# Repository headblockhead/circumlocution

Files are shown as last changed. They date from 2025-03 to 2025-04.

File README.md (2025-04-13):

# Circumlocution

> the use of many words where fewer would do, especially in a deliberate attempt to be vague or evasive.

Welcome to maker hell, where we have all the parts of a broken Ender 3 clone, none of the time, a copy of FreeCAD, and an unhinged desire to watch an overcomplicated 3D printer spin.

## Build Guide

You should not build this printer. That's probably not something you would usually read in a project's README, but it's true.

I designed this printer to make something out of the assorted scraps of parts and frame left over from a dissasembled Sovol SV01 (Ender 3 clone with direct drive), and ideally something that looked funny or cool, hence the spinning bed. 

99% of decisions were based on what I had, or what I could buy cheaply, so some part selections or fastener choices are very strange.

If you also have some random Ender 3 related printer parts around the place, this project might work for you, but I guarentee that you will need to change some elements of the design, and you are best off making something else with the parts.

## How? Why?

1. Around 50 hours of hard work
2. Because I thought it would be funny, and I wanted to join in with [hackclub's infill project](https://github.com/hackclub/infill).

I chose FreeCAD because:
  1. I hate it when people's projects require people to beg/borrow/steal/leagally-buy Autodesk Fusion 360 access just to see or modify them
  2. I wanted to become more familliar with how FreeCAD works.

I may revise/re-make this project into something more complete with a followable build guide and a better design (EG. lots of X-space could be saved on the extruder design, a longer alu. extrusion could add a second Z axis, etc.) someday.

## CAD Gallery

Yes, the rectangular bed spins.

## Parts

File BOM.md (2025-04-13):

# BOM

(cables and fasteners not currently included)
(TODO: pricing)

- [ ] Turntable/lazy susan/bearing
- [ ] Orbiter v2.0
- [X] 4x NEMA 17 motors
- [X] 2x 5-8mm Z coupling
- [X] 2x 430mm(?) Lead screws
- [X] 2x lead screw nuts
- [X] 2x GT2 20tooth pulley
- [X] 1x MeanWell LRS-350
- [ ] 1x BLTouch
- [ ] 1x E3D v6 Hotend
- [ ] 2x 3010 fans (noctua?)
- [X] 1x SKR mini E3
- [X] 12x 2020 V-slot wheels
- [X] 2x 410mm 2040 extrusion (left+middle)
- [X] 2x 470mm 2040 extrusion (Z-axis)
- [X] 3x 400mm 2020 extrusion (top+bottom+X-axis)
- [X] 1x 450mm 2040 extrusion (right)

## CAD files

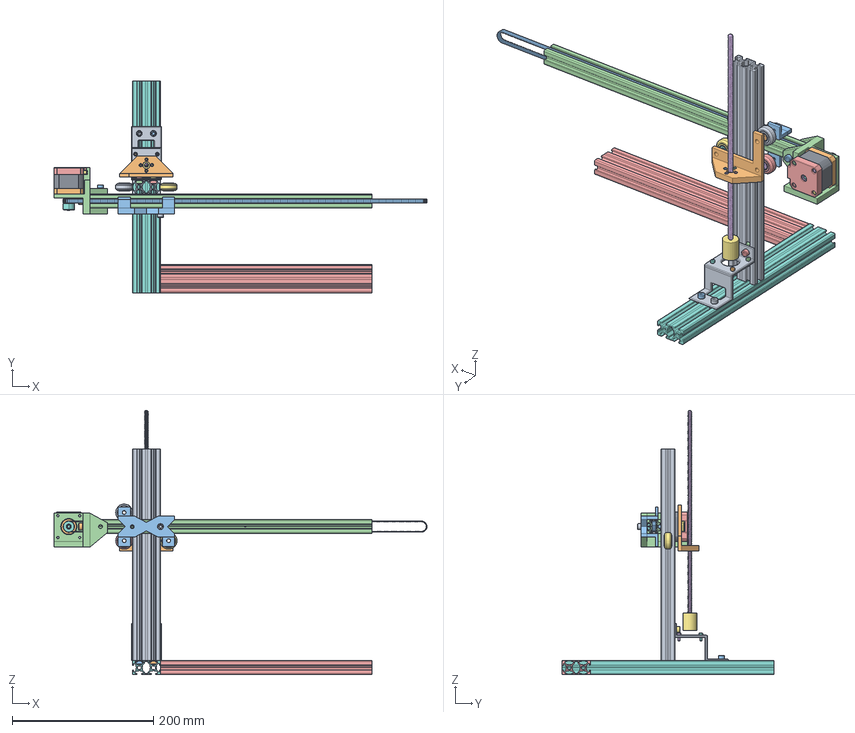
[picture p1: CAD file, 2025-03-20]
circumlocution.FCStd
528.9 x 300.0 x 375.0 mm
ZMotorBracket
M5 x 20 series-TSlot
M5 x 20 series-TSlot005
M5 x 20 series-TSlot007
M5 x 20 series-TSlot006
M3x8-Screw
M5x6-Screw
M3x8-Screw021
M5x6-Screw012
M3x8-Screw022
M5x6-Screw013
M3x8-Screw023
M5x6-Screw014
6x300-ThreadedRod
Z-5-8mmCoupling
BaseLeftExtrusion
ZAxisExtrusion
BackZFollower
M3x5.74-Insert
M3x5.74-Insert244
M3x5.74-Insert245
M3x5.74-Insert246
M5 x 20 series-TSlot016
M5 x 20 series-TSlot017
M5x12-Screw001
M6x20-Screw
M5x12-Screw
XAxisExtrusion
rear end cap001
rear bearing001
connector001
shaft001
stator001
front end cap001
front bearing001
M3x10-Screw004
M3x10-Screw005
M3x10-Screw006
M3x10-Screw007
GT2 Pulley 20 Tooth (ID6mm)
socket set screw flat point_am_B18.3.6M - M3 x 0.5 x 5 Hex Socket Flat Pt. SS --S
socket set screw flat point_am_B18.3.6M - M3 x 0.5 x 5 Hex Socket Flat Pt. SS --S001
PathArray
6153K690_625-2RS SST BALL BEARING, SEALED v2
6153K690_625-2RS SST BALL BEARING, SEALED v003
6153K690_625-2RS SST BALL BEARING, SEALED v004
6153K690_625-2RS SST BALL BEARING, SEALED v005
6153K690_625-2RS SST BALL BEARING, SEALED v006
6153K690_625-2RS SST BALL BEARING, SEALED v007
6153K690_625-2RS SST BALL BEARING, SEALED v008
6153K690_625-2RS SST BALL BEARING, SEALED v009
6153K690_625-2RS SST BALL BEARING, SEALED v010
6153K690_625-2RS SST BALL BEARING, SEALED v011
6153K690_625-2RS SST BALL BEARING, SEALED v012
6153K690_625-2RS SST BALL BEARING, SEALED v013
6153K690_625-2RS SST BALL BEARING, SEALED v014
6153K690_625-2RS SST BALL BEARING, SEALED v015
6153K690_625-2RS SST BALL BEARING, SEALED v016
6153K690_625-2RS SST BALL BEARING, SEALED v017
6153K690_625-2RS SST BALL BEARING, SEALED v2 (1)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

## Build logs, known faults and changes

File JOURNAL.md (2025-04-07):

Made by: @Edward Hesketh
Repository link: https://github.com/headblockhead/circumlocution/
Total hours so far: 50

- [x] I have a 3D printer or will be getting one before March 21st

# Circumlocution Journal

A documentation of the process of designing, modelling, and making my polar printer for [Hack Club's Infill YSWS](https://infill.hackclub.com/).

## Hour 1

<sup>began on UNIX Timestamp 1739815200</sup>

## Design sketch 

I started drawing up a design sketch for what my printer could look like using GIMP, and came up with a design I was happy with.
(15 mins)

A4 first-draft design drawings

Then, I started planning out the rough mechanical design for how the printer's motors would be positioned.
(20 mins)

A4 hand-drawn rough mechanical design

I took a few measurements from the ender 3, and did a little research, and decided on 2020 aluminium extrusion to use for the frame, and M10 threaded rod for the Z-axis. I have a feeling that these decisions might change later, but for now, that's what I'll use for the CAD models. I'm thinking of using FreeCAD for the printer, but I'm pretty sure I'll regret it 😆! I also researched the time+date of the Rocky Mountain RepRap Festival to ensure I could actually make it there, without missing too much schoolwork or any exams that I'd have to do tons of catch-up for. Hopefully, if I make it, my school will allow me to take a day or two off to attend.
(25 mins)

## Hour 2

<sup>began on UNIX Timestamp 1739819370</sup>

I started modelling the 2020 extrusion in FreeCAD for use in my design based on this reference diagram from [www.tnutz.com](https://www.tnutz.com/product/exm-2020/).

The reference image for the 2020 extrusion

This is the end result:

FreeCAD Sketch showing the 2020 extrusion's cross-section
FreeCAD screenshot showing the extrusion, extruded

(60 mins)

## Hour 3

<sup>began on UNIX Timestamp 1739885638</sup>

I started modelling the Z axis. I looked at the design of the Ender 3 for an example of how a Z-axis could be assembled:

Ender 3 Z-Axis picture

And I moddled some 2040 extrusion.

2040 extrusion model

I also sourced [a model for a NEMA 17 stepper motor](https://www.thingiverse.com/thing:6761583/files), to use as reference for the 3D printed parts.

NEMA 17 stepper screenshot

Finally, I generated a model for the threaded rod - a TR8x8 lead screw (30cm).

Lead screw model

## Hour 4

<sup>began on UNIX Timestamp 1739889914</sup>

I found [an existing NEMA 17 motor mounting bracket](https://www.123-3d.co.uk/123-3D-Metal-mounting-bracket-for-NEMA17-stepper-motor-90-L-bracket-i2129-t14804.html) made of sheet metal, and modelled it to see if it could fit the 2040 extrusion. I spent 50 minutes creating the model, but it isn't compatible with the 2040 rails, it just looks like it *could* be. Oh well! Looks like I'll have to design a part for this bit. At least I have accurate dimensions though!

NEMA 17 motor mount

I've had no regrets using FreeCAD so far, the 1.0.0 version improved a **lot** since ~0.2. Fusion 360 would be *way easier*, but it's not exactly in the 'open source spirit' in my opinion, because if Fusion dies, the project dies too. But FreeCAD's code will (hopefully) be available for free, and for forever. 

I'm keeping the right angle bracket model around just in case I am able to use it somewhere else, I'm getting my time's worth out of that model someday!

I also found [some brackets](https://www.123-3d.co.uk/123-3D-Blind-corner-connector-for-aluminium-2020-profile-123-3D-brand-i1590-t14575.html) for attaching the extrusions together, could be worth a look at next hour.

## Hour 5

<sup>began on UNIX Timestamp 1739893575</sup>

I modelled the 5-8mm shaft coupling part:

coupling part

And created the first 3D-printable part, the mounting bracket for the motor.

motor mounting bracket

## Hour 6

<sup>began on UNIX Timestamp 1739897976</sup>

I have found the correct sizes of fasteners (nuts/bolts/TSlots) for the rails and motors that I am using, and have added them to the CAD model, in roughly the correct places, to ensure that my parts don't overlap the heads of any of the screws I will need to install.

motor and extrusions with screws and slots

Finally, I renamed all of the parts to have (mostly) sensible names:

parts list with sensible names

## Hours 7-9

<sup>hour 7 began on approx. UNIX Timestamp 1740168000 and 8-9 on approx. UNIX Timestamp 1740256200</sup>

I have made quite a lot of undocumented progress on-and-off through short sessions in my free time, so in summary the changes are:
- Added a trapezoidal nut to follow the lead screw
- Switched to using hex bolts instead of phillips screws
- Set the position of objects manually, to avoid imprecision from visual only alignment
- [Found a pulley](https://www.123-3d.co.uk/123-3D-GT2-high-resolution-timing-belt-pulley-20-teeth-6mm-belt-5mm-bore-GT2-20T-W6-B5-i2081-t14815.html) for the X axis belt, [and a similar-enough model](https://grabcad.com/library/gt2-pulley-20-tooth-id-6mm-1)
- Built a carriage to follow the nut by holding the nut using screws screwing into heat-set inserts

a screenshot of the whole assembly with changes as described above

## Hour 10

<sup>began on UNIX Timestamp 1740416875</sup>

I planned out the position for the rollers to follow the Z axis:



Added the rollers, and started re-building the carriage.



## Hours 11-16

<sup>took place across multiple days between timestamps 1740416875 and 1741539544</sup>

I re-built the entire Z-following carriage into two 3D-printable parts, held together with insertable nuts and screws.

(as seen from front side)



(as seen from back side)



## Hours 17-20

<sup>took place across multiple days between timestamps 1741539544 and 1742252892</sup>

I moddled a holder to keep the X motor in place, added a belt and coupler, and connected the end of the extrusion to the X motor holder with an M6 screw to prevent the X rail from sliding through the Z follower.



## Hours 21-50

<sup>took place across the months of March and April 2025, hour count estimated - unknown</sup>

I accidently finished most of the printer without writing a single journal entry. (oops!)

I also just came up with the tagline to sum up this whole experience so far:

> Welcome to maker hell, where we have all the parts of a broken Ender 3 clone, none of the time, a copy of FreeCAD, and an unhinged desire to watch a 3D printer spin.

I think it really captures the feeling of 'what do I do now?' after just disassembling a printer into parts, and realising you have to CAD it all back together into a functional design.

Most choices made during the design process were based on what I had lying around from my old printer (the Sovol SV01), what was availiable on AliExpress, and what was easiest to 3D model.

Considering this is my first 'real' CAD project, I'd say I did an OK job. Perhaps if I was to redesign it, I'd use linear rails, or various better options than the old parts of a broken printer. It would've opened me up to making a better, more unique, and more functional design, but would've cost significantly more. Maybe once I've finished building it I'll re-assemble the parts back into the Ender 3 clone it used to be. We'll see.

The due date of the design was March 31st, but I overran into April 7th, finishing a few hours before last call.

I don't have high hopes for this project.



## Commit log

2025-02-17 chore: add FreeCAD files
    [circumlocution.FCStd]
2025-02-18 feat: add freecad and image files for hours 3-4
    [circumlocution.FCStd]
2025-02-23 feat: add files and updates for steps 7-9
    [circumlocution.FCStd]
2025-02-24 feat: add Hour 10 file
    [circumlocution.FCStd]
2025-03-09 feat: add FreeCAD files for hours 11-16
    [circumlocution.FCStd]
2025-03-17 feat: add freecad files for hours 17-20
    [circumlocution.FCStd]
2025-03-20 feat: push latest changes, WIP
    [circumlocution.FCStd]
2025-03-24 feat: add latest FreeCAD files
    TODO: update JOURNAL.MD with latest changes
    TODO: work on extruder body
    TODO: work on buildplate (custom PCB?)
2025-04-06 feat: add... most of the rest of the printer
    oops! Forgot to commit the last few week's worth of changes.
2025-04-06 feat: add bed components
2025-04-13 docs: init BOM
